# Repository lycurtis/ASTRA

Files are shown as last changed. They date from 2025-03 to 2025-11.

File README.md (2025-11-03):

# ASTRA - Autonomous System for Tracking, Reconnaissance, and Assistance
An open-source UAV platform for search-and-rescue (SAR) that combines real-time human detection, waypoint navigation, and ground-station visualization


ASTRA

## Table of contents
- [What is ASTRA](#what-is-astra)
- [Core Capabilities](#core-capabilities) 
- [System Architecture (High Level)](#system-architecture-high-level)
- [Key Specs & Design Targets](#key-specs--design-targets)
- [Demos](#demos)
- [How It Works (Data Flow)](#how-it-works-data-flow)
- [Testing Highlights](#testing-highlights)
- [Team](#team)

## What is ASTRA?
ASTRA is a semi-autonomous quadrotor designed to improve SAR operations. It flies in versatile environments, detect humans on-board using AI, and relays detections + GPS coordinates to a ground station UI for immediate response. ASTRA is the better alternative as it is a targeted, low-cost research platform that bridges manual piloting and intelligent rescue tooling.

## Core Capabilities 
- `On-board computer vision (YOLOv8):` Real-time human detection (single class: person) driven by NVIDIA Jetson Orin Nano + Luxonis OAK-D-Lite depth camera.
- `Waypoint/simulated autonomy:` Routes planned in QGroundControl (Pixhawk 4/PX4 Firmware).
- `Live communication:` Detections and telemetry to the ground station over UDP/Wi-Fi; MavLink telemetry maintained over RF
- `Ground-station UI:` Camera feed, Google Maps GPS view (online) with Offline Mode feedback map when there's no internet

## System Architecture (High Level)
ASTRA is split into UAV and Ground station subsystems:
- **UAV:** Pixhawk 4 (flight), M10 GPS, OAK-D-LITE
- **Ground Station:** Python/Tkinter UI showing detections, map, and terminal telemetry; live stream via Flask
### Highlight
- GPS --> Jetson (Processing + CV) --> UDP --> UI
- RF telemetry is maintained in parallel
- I2C/USB/UART form the internal peripheral backbone, and UDP carries time-sensitive events

## Key Specs & Design Targets
- **Flight Path**: Waypoint navigation, 9-10 ft altitude, 5 mph parameter set
- **Range (control/telemetry):** ~427 ft effective radius (validated)
- **Vision performance:** 20-25 FPS camera output; <= 800 ms end-to-end latency target
- **Detection Range:** ~50 m (person)
- **Power/Weight:** 4S 3300 mAh LiPo; total takeoff weight ~2.5 kg (5.5 lb)
- **Alert cadence:** 2 Hz SOS updates on detection

## Demos
Project clips:
- Flight & platform overview: https://youtu.be/dsUHsBSHA0g
- Ground-station & detections: https://youtu.be/vNRCC04JXCo

## How It Works (Data Flow)
1. `astra.py` boots the pipeline on the Jetson
2. `human_detect.py` processes OAK-D-Lite frames w/ YOLOv8 and logs `DETECTED`/`NOT_DETECTED`
3. `sos_transmitter.py` tails the log and transmits detection state via UDP to the ground station at the configured IP:5005 (de-duped on state change)
4. `astraui.py` from the ground station receives UDP, renders camera, map, and terminal; includes an **Offline Mode** map when the internet is unavailable

## Testing Highlights
- **RF control range:** Stable up to ~427 ft (two environments)
- **UDP comms:** Transmitter and receiver validated; terminal shows “PERSON DETECTED” / “Searching for persons…” on packets
- **Latency & video:** Bounded queue eliminated stale frames and reduced perceived lag in the UI
- **EMI mitigation:** Camera + USB 3.0 near GPS caused lock loss; shielding, grounding, cable reroute, and ferrites restored stable lock
- **Prop selection:** 1147 props chosen for best balance of lift/stability vs. 1045/1245

## Team
### Benjamin Kim
Main: Computer Vision (YOLOv8), PersonID

### Curtis Ly
Main: Hardware, System Architect 

### Pryce Matsudaira
Main: User Interface, PersonID

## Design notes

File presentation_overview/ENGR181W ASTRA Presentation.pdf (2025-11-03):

# ASTRA

Benjamin Kim, Curtis Ly, Pryce Matsudaira

# The Autonomous System for

Tracking, Reconnaissance,

# and Assistance

## 1) Problem Statement

## 2) Objectives

## 5) Innovation & Technical Depth

## 3) Design Approach

## 6) Limitations & Future Work

## 4) Implementation & Results

# Table of Contents

- Delays can determine life and death

## 3) Real-World Impact

- Search and Rescue (SAR) in unpredictable environments
- Need quick detection and response
- SAR systems rely on manual input
- Response time puts humans at risk
- Robotic support for human rescuers
- Minimizes human effort & maximizes response efficiency

# Demand for Autonomous Rescue Detection

## 1) The Problem

2) Current Limitations | 4) Solution

- Real-Time human detection
- Maintain accuracy
- Autonomous navigation
- Transmit alert signal with low latency

# Goals and Objectives

Problem Identified | ASTRA Objectives
Slow Human Detection | YOLOv8
Latency | On-board AI processing
Manual Labor | QGroundControl Autonomy

# Hardware System Integration

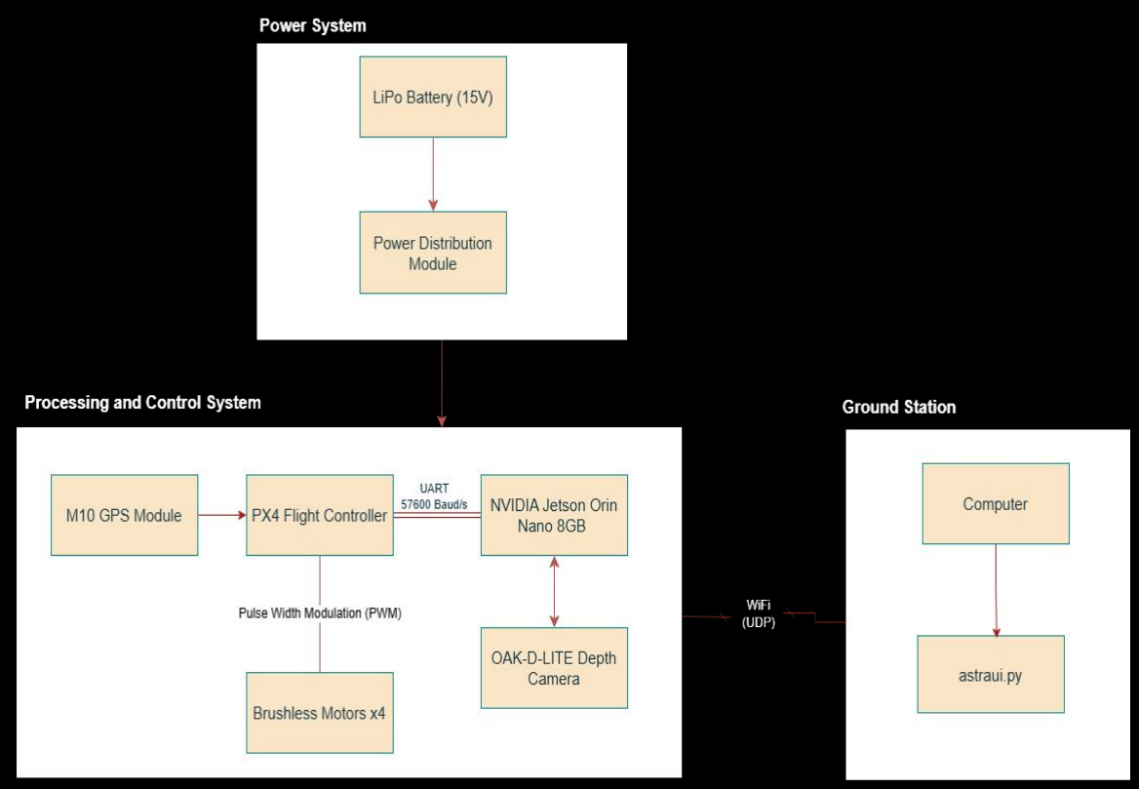
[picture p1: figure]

# Functionality

1) Power Distribution
2) Flight Control
3) Onboard Processing
4) Wireless Communication
5) Ground Station

# Software System Integration

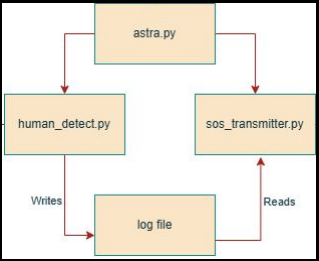
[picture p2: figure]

## Methodology Process

## 1) Object Detection Selection

## 4) Test and Improve

## 2) Vision Pipeline Integration

## 5) Final Integration

## 3) Communication Interface

### - UAV followed predefined routes

# Implementation & Results

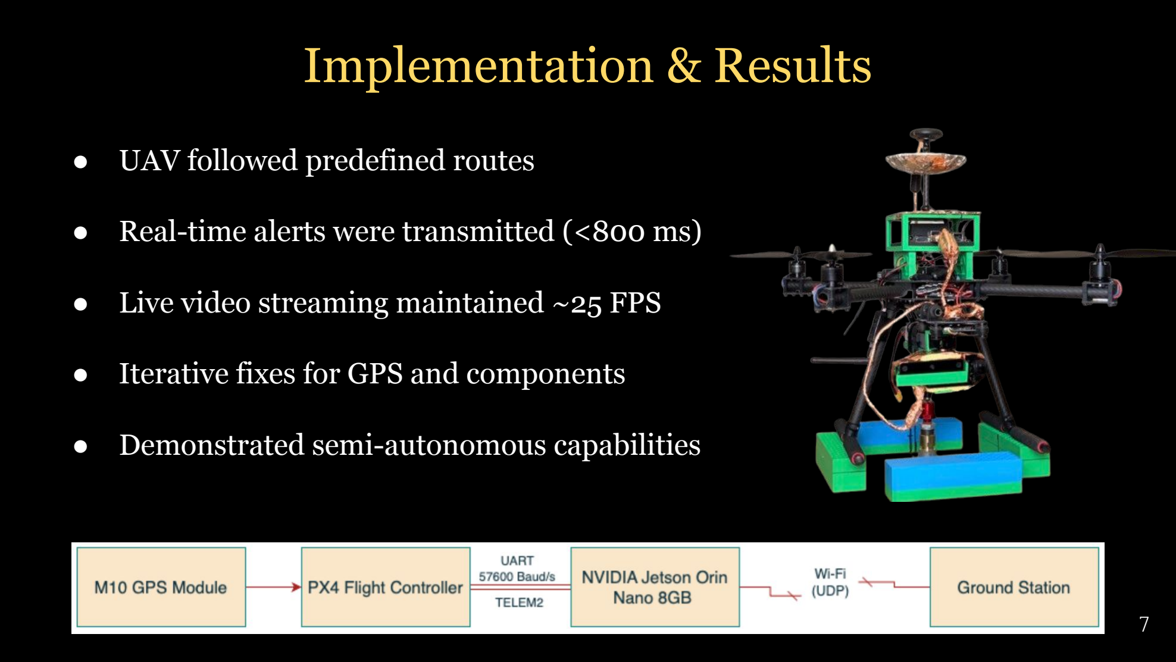
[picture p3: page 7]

### - Real-time alerts were transmitted (<800 ms)

### - Live video streaming maintained ~25 FPS

### - Iterative fixes for GPS and components

### - Demonstrated semi-autonomous capabilities

## - Improve video latency and resolution

## - Wi-Fi Dependency Workaround

## - Integrate Person Differentiation

## - Implement full autonomy

## - Flight Duration

# Limitations & Future Work

# Thank you

Benjamin Kim, Curtis Ly, Pryce Matsudaira

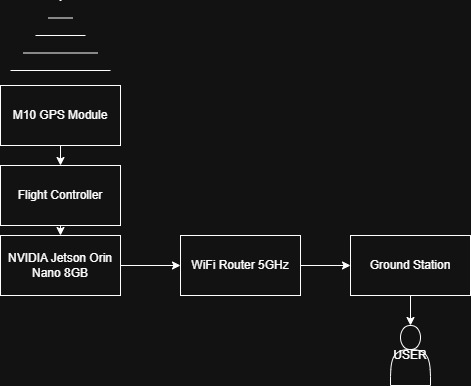
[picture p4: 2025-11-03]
system_charts/HighLevelArchitecture.jpg

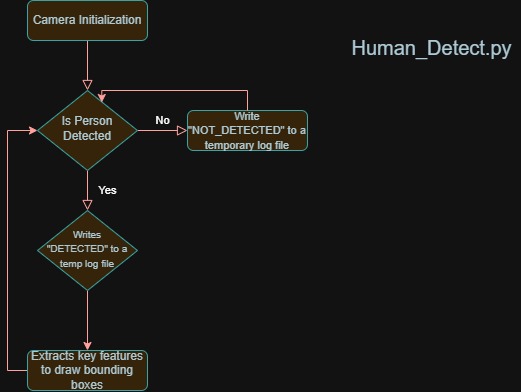
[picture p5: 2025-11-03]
system_charts/HumanDetect.py.jpg

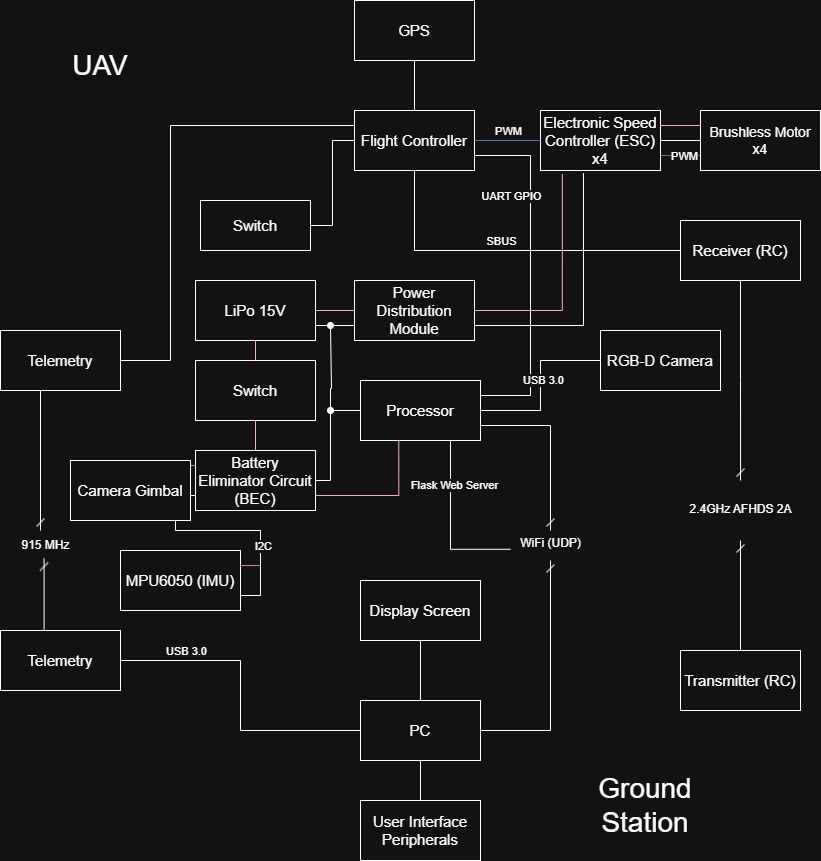
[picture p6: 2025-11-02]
system_charts/SystemBlockDiagram.jpg

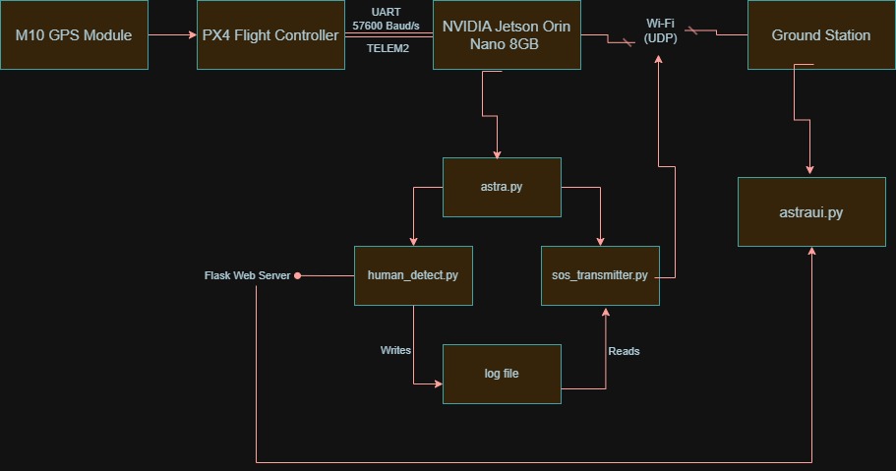
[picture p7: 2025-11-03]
system_charts/Functional_Flowchart.jpg

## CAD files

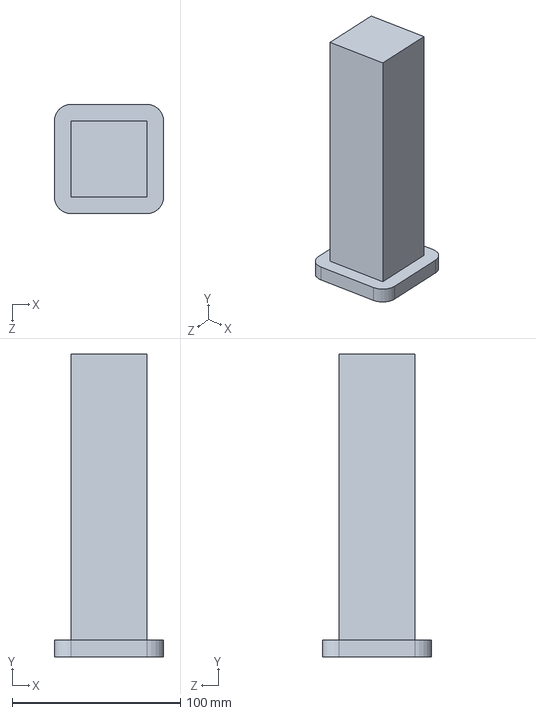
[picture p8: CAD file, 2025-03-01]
CAD/motor_level/motor_level_fullstand.SLDPRT
65.0 x 180.0 x 65.0 mm

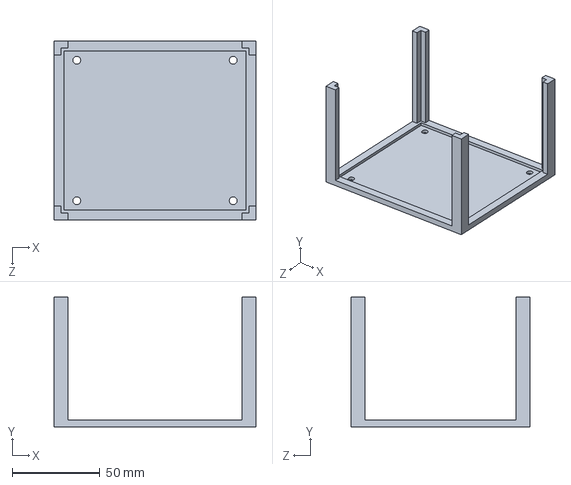
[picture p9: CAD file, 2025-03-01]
CAD/jetson/Jetson and LiDAR mount.SLDPRT
115.0 x 74.0 x 102.0 mm

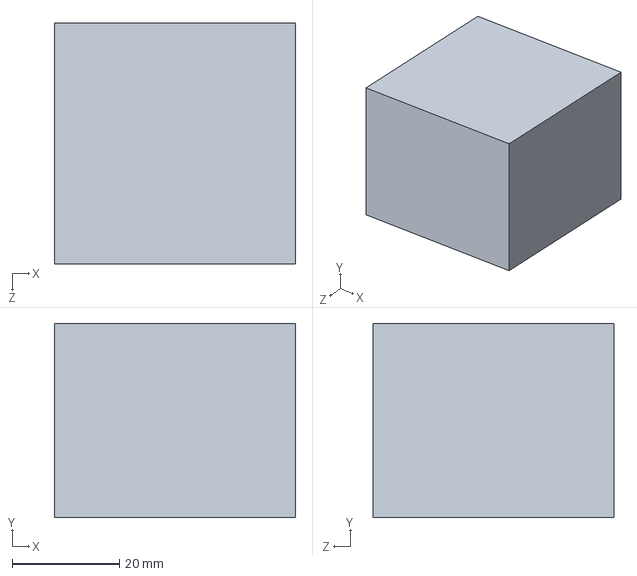
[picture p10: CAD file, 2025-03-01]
CAD/motor_level/2.SLDPRT
45.0 x 36.3 x 45.0 mm

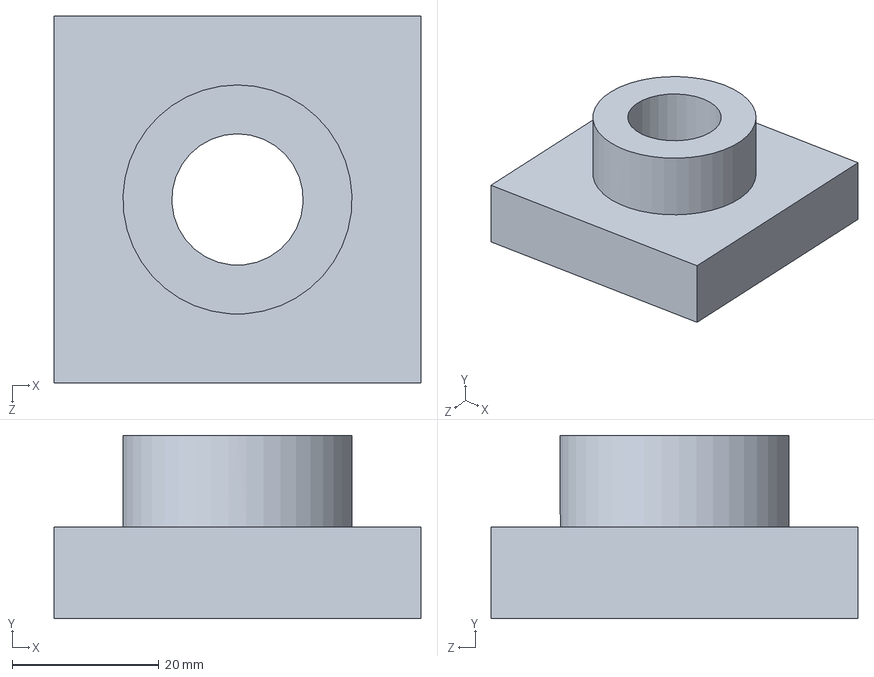
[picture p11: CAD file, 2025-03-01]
CAD/test_rig/testrigslot.SLDPRT
50.0 x 25.0 x 50.0 mm

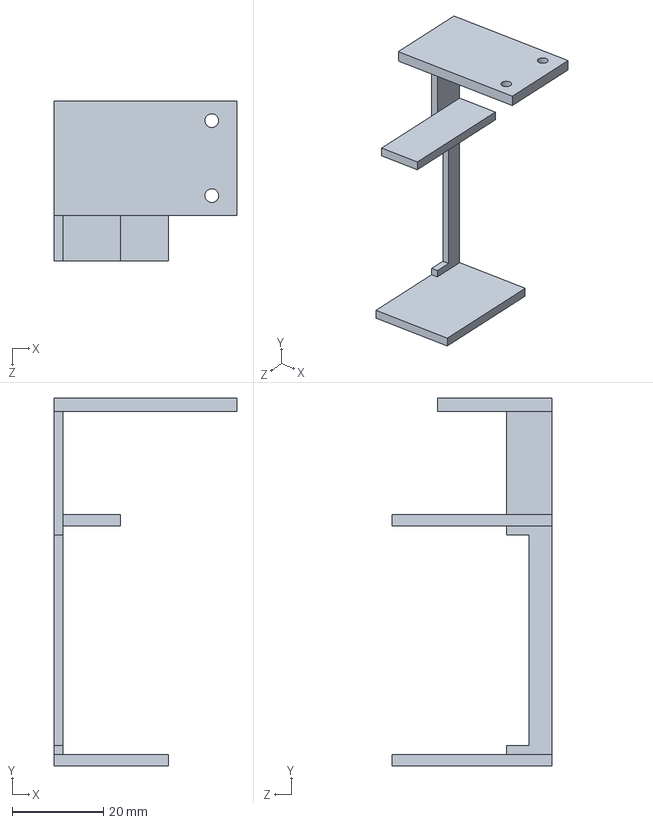
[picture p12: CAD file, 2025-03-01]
CAD/jetson/Gimbal Support.SLDPRT
40.0 x 80.5 x 35.0 mm

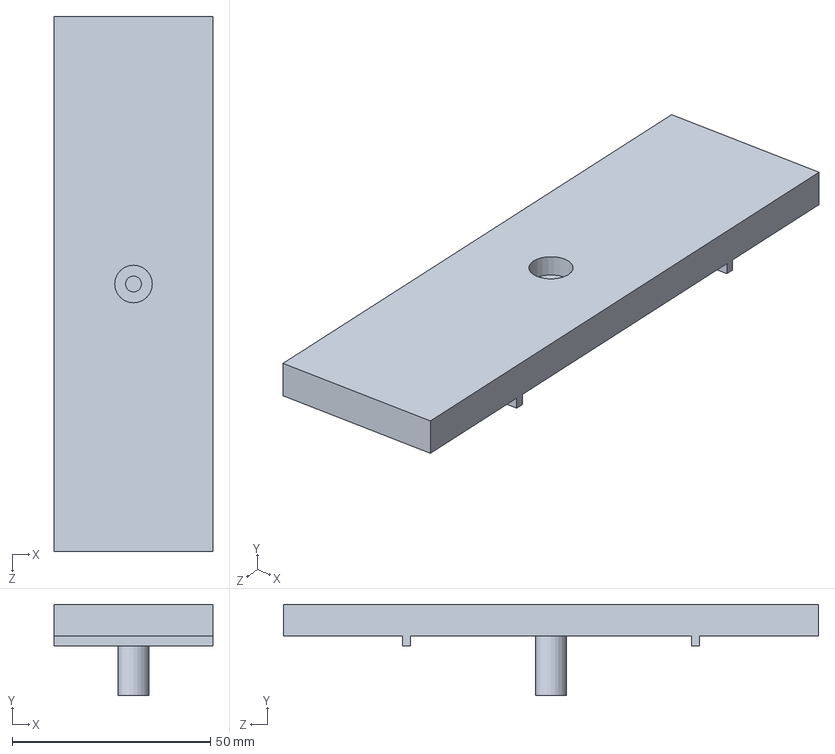
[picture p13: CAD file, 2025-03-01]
CAD/test_rig/ball swivel attachment.SLDPRT
40.0 x 23.0 x 135.0 mm

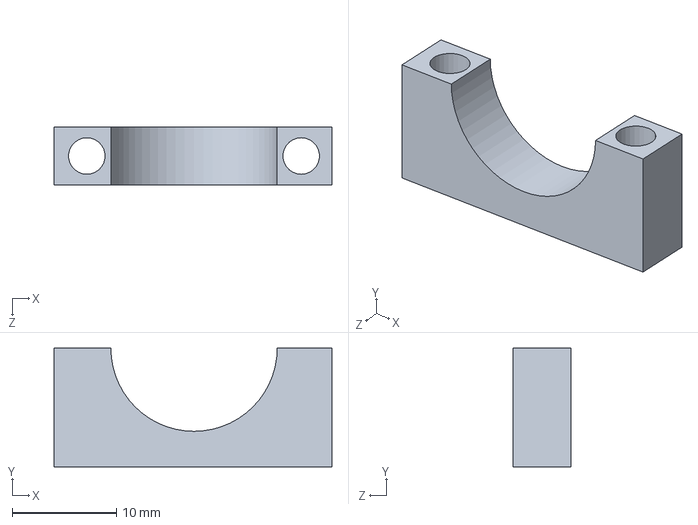
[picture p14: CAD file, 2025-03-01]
CAD/jetson/Arm Strap.SLDPRT
26.6 x 11.4 x 5.52 mm

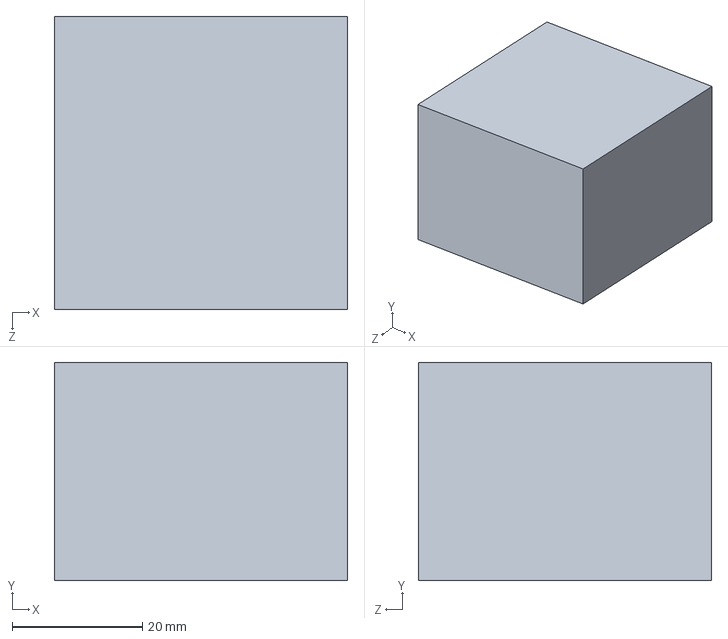
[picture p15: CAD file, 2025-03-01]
CAD/motor_level/motor_level_attachment.SLDPRT
45.0 x 33.5 x 45.0 mm

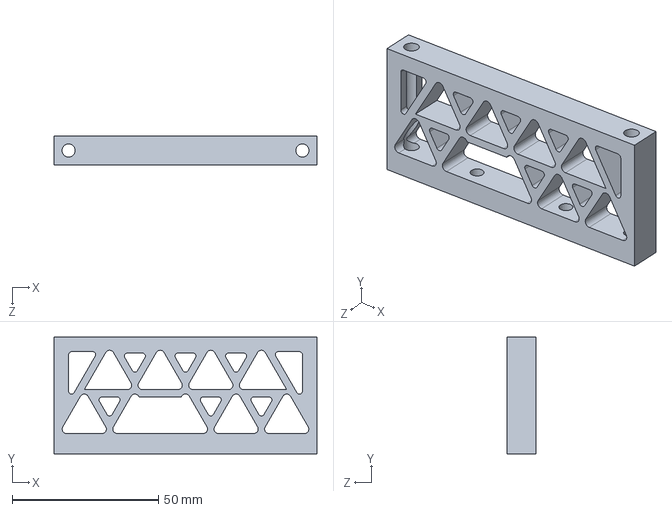
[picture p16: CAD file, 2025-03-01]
CAD/jetson/leg.SLDPRT
90.0 x 40.0 x 10.0 mm

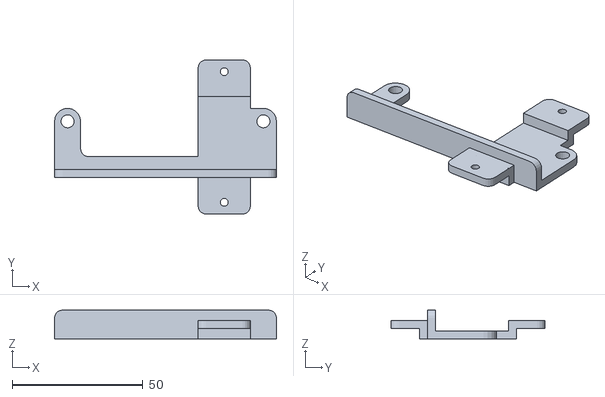
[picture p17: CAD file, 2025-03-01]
CAD/jetson/OAK-D Lite Gimbal Mount.stl
85.0 x 59.0 x 11.0

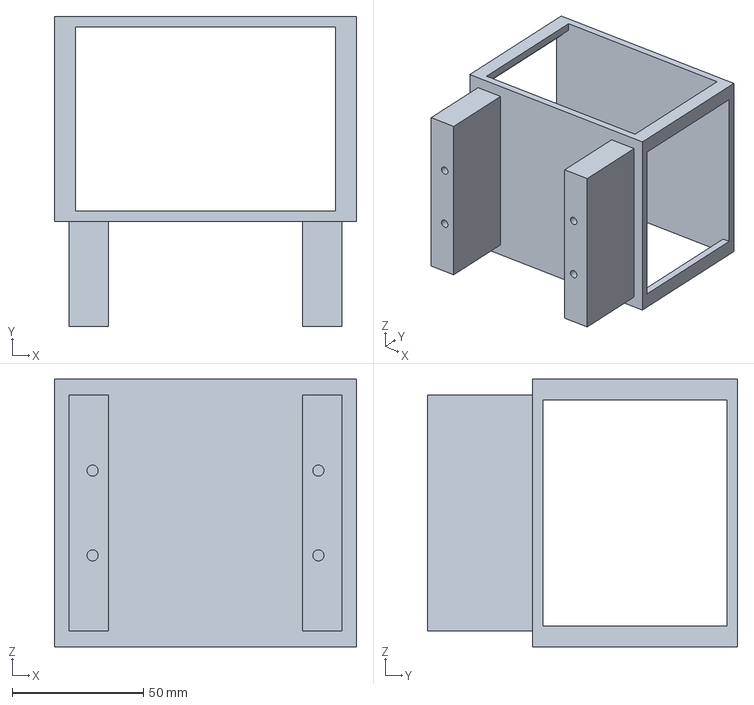
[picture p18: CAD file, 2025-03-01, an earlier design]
CAD/jetson/archive/Jetson and LiDAR mount.3MF
115.0 x 118.0 x 102.0 mm

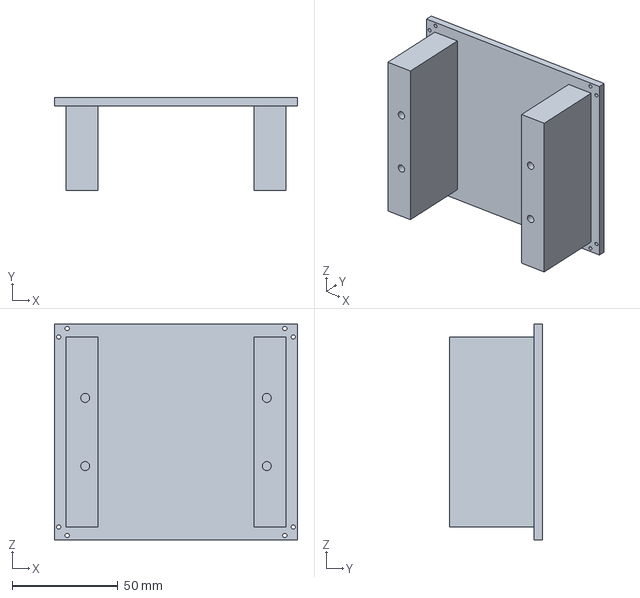
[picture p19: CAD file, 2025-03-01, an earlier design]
CAD/jetson/archive/Jetson mount.3MF
115.0 x 44.0 x 102.0 mm

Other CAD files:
CAD/jetson/archive/LiDAR mount.SLDPRT
CAD/jetson/Arm Strap.3MF
CAD/jetson/Gimbal Support.3MF
CAD/jetson/archive/LiDAR mount.3MF
CAD/jetson/leg.3MF
CAD/motor_level/2.3MF
CAD/motor_level/motor_level_attachment.3MF
CAD/motor_level/motor_level_fullstand.3MF
CAD/test_rig/ball swivel attachment.3MF
CAD/test_rig/testrigslot.3MF

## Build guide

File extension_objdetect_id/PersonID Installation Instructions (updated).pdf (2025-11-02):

# GPU-Accelerated Human Differentiation Network

Pryce Matsudaira & Benjamin Kim

Project Overview
This project implements a real-time detection and identification system for specific individuals. ASTRA (our senior design drone project) detects all people in a video feed using a pre-trained YOLOv8 model. The core objective of this project is to extend ASTRA’s scope to accurately detect specific people in a video stream and differentiate them by comparing visual features to a gallery of precomputed identity embeddings. To achieve this, we utilized a fine-tuned ResNet18 system for generating person-specific vector embeddings. Cosine similarity (via a custom CUDA kernel) is then used to compare those embeddings with a vector that represents the individual (e.x, differentiating between Ben and Pryce).

How the GPU is Used to Accelerate the Application
The GPU is used to accelerate the cosine similarity computation. When an individual is detected by a web camera, their ResNet18-generated feature vector is compared with a gallery of that individual’s stored embeddings. To make this comparison process efficient, a custom CUDA kernel is used to parallelize the cosine similarity calculations.
Our parallel algorithm is structured so that the query embedding is compared against all gallery embeddings at the same time. Each GPU thread computes the cosine similarity between those two vectors. Additionally, each thread also computes the similarity score for one gallery embedding, with 256 threads in one thread block. To ensure all gallery embeddings are executed, the grid size is set as the ceiling of the number of gallery embeddings divided by the thread block size. This allows for the similarity scores of N gallery embeddings to be computed in parallel within one kernel launch. The person identification stage of the software pipeline is parallelized.

Implementation Details
Each team member recorded two videos of themselves: one focused on their face (close-up) and another focused on their entire body. OpenCV was then used to extract frames from the videos at 5-frame intervals. Of those frames, the 10 best lighting and resolution images were manually selected and processed through a ResNet18 embedding model to extract a 512-dimensional feature vector. The vectors for each individual were averaged to create a gallery embedding for later use.

The implementation process of human_differentiation.py begins with real-time human detection via a YOLOv8 object detection algorithm, which had to be re-implemented for a desktop or laptop webcam through OpenCV. This was because the previous implementation for YOLOv8 on ASTRA relied on the compatibility with the drone’s depth camera drivers through Linux. Frames from a web camera will pass through YOLOv8 and output bounding boxes around detected humans. YOLOv8 will use such bounding boxes to crop regions of the detected individual and pass them through a pretrained ResNet18 model. The model will output a 512-dimensional feature vector of the individual’s visual features.
The script then ideally loads a compiled Parallel Thread Execution file with a CUDA kernel for efficient and fast cosine similarity computation. However, due to complications discussed later, the cosine similarity kernel had to be created and directly implemented in the human_differentiation.py script using Numba. A ResNet18 model is initialized as somewhat of an embedding extractor and deployed on the GPU. As mentioned earlier, Pryce and Ben each have stored image embeddings, which are loaded and organized into a NumPy array.
When a human is detected from the web camera, a ResNet18 model analyzes a cropped region of the detected individual and converts it into a 512-dimensional embedding vector. This vector analyzes the visual features of the individual and compares them against precomputed averaged embeddings using cosine similarity. Each thread calculates similarities between the ResNet18 embedding and the gallery embedding, allowing one-vs-many comparisons in a kernel launch.
If the calculated similarity score is higher than the defined threshold of 0.55 or 55%, the system will label the predicted human accordingly above their bounding box. If no match was detected, the system will label “Unknown Person”. This human differentiating system utilizes deep learning models, computer vision algorithms, and GPU acceleration to detect and label individuals.

Installation/Setup Process
1) Install Python (3.12 or higher) and required libraries, including opencv-python, numpy, numba, torch, cuda-python, torch, pillow, and ultralytics. Additionally, make sure the NVIDIA CUDA Toolkit (12.9) is installed and that NVIDIA GPU drivers are up to date.

2) First, upload video files of yourself and the people you want to differentiate to Google Drive. (Ex. My Drive → person_videos → pryce, ben)
a) Google Drive was mainly used to store datasets and videos for this project due to compatibility issues with each script on respective laptops/desktops. Not all laptops/desktops have the same file paths C:\User\etc\etc, which would require us to change the code every time to create dataset updates. Google Drive also allows you to share these videos and datasets easily
b) Example Image(s):

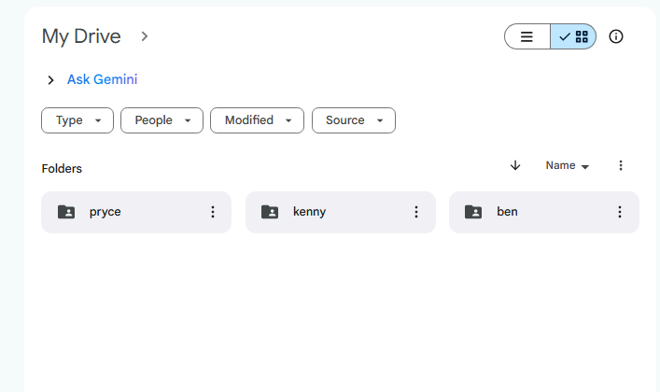
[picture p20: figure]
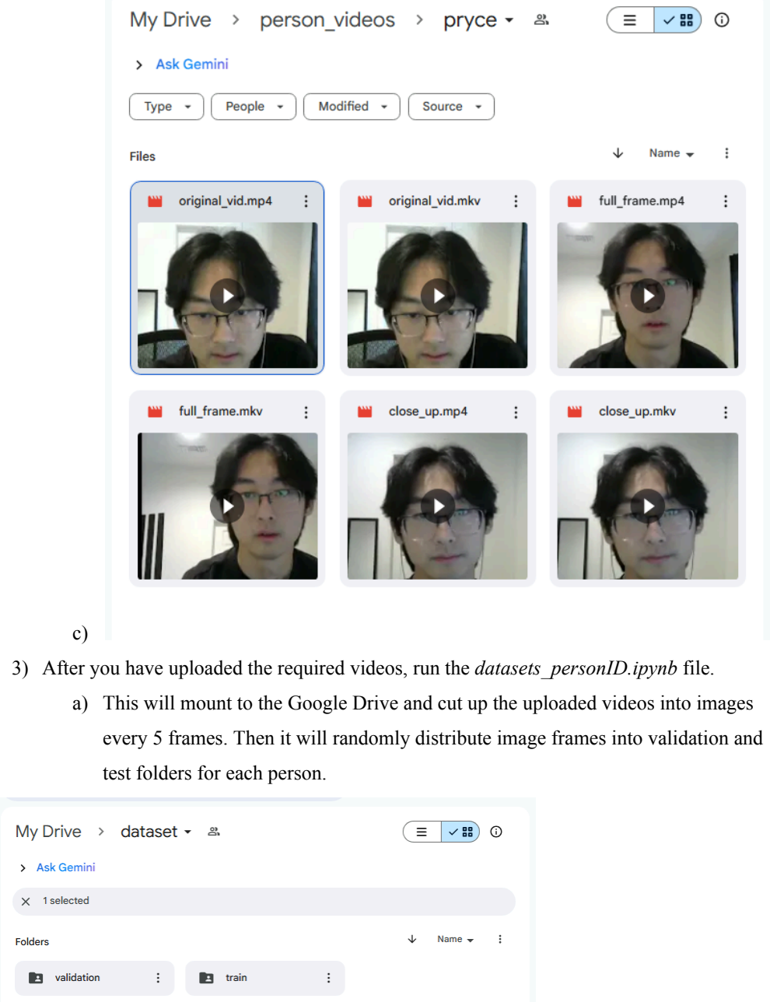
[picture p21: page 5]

c)
3) After you have uploaded the required videos, run the datasets_personID.ipynb file.
a) This will mount to the Google Drive and cut up the uploaded videos into images every 5 frames. Then it will randomly distribute image frames into validation and test folders for each person.

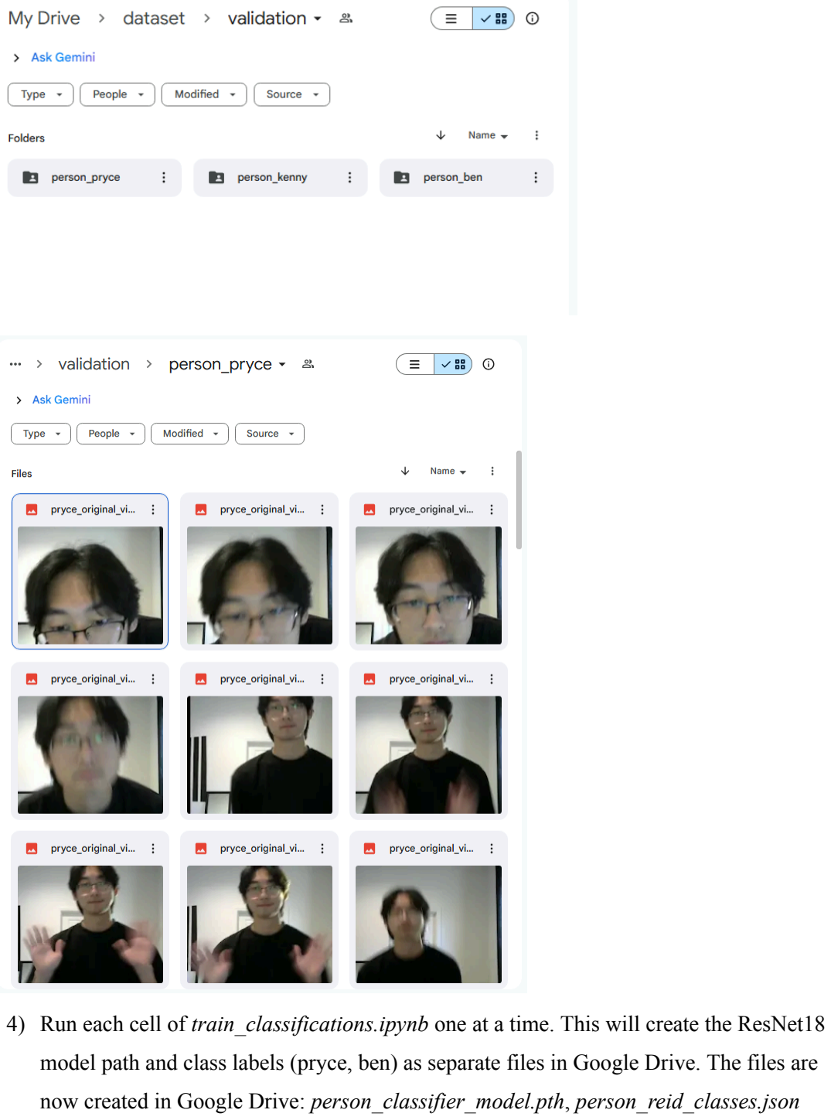
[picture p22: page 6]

4) Run each cell of train_classifications.ipynb one at a time. This will create the ResNet18 model path and class labels (pryce, ben) as separate files in Google Drive. The files are now created in Google Drive: person_classifier_model.pth, person_reid_classes.json a) Each cell will set up the classifier, loss function, and optimizer for classification, training loop, then classification model training (Epochs train loss/accuracy and validation loss)
5) Run each cell one at a time for embeddings_personID.ipynb. This file will begin building the ResNet18 model and initializing previously created weights. It will then extract features into a vector embedding. You will then test the shape and viability of the extracted embedding.
a) You will then manually input each image name from the validation folder “ben_IMG_7093_frame_00370.jpg” 10 times for each person you want to create an average embedding vector of.
6) You will then need to take person_classifier_model.pth and person_reid_classes.json files from Google Drive and import them to your specific computer.
7) Ensure folders and files are organized for proper file paths
- models/ (ResNet18 Models)
- person_classifier_model.pth
- person_reid_classes.json
- gallery_embeddings/ (Averaged embeddings of specific individuals from embeddings_personID.ipynb)
- ben_gallery_embedding.npy
- pryce_gallery_embedding.npy
- scripts/
- yolov8n.pt
Example Image:
8) Make sure to have your Python (3.12+) installation in the same directory as human_differentiation.py

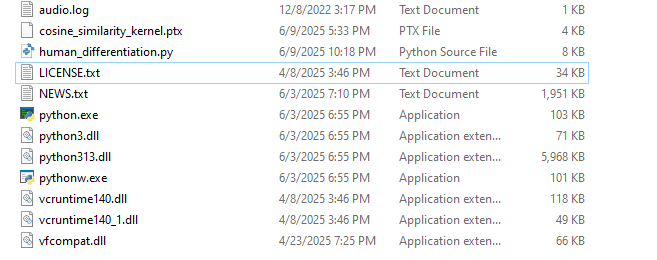
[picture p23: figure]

9) Make sure cosine_similarity_kernel.cu is in the PersonID folder or in a file that has administrator access. Now convert cosine_similarity_kernel.cu to a PTX file.
a) Open Developer Command Prompt for VS 2022 then input cd C:\YourPath\PersonID —> nvcc -ptx -ccbin "C:\Your\Full\Path\To\MSVC\bin\Hostx64\x64" cosine_similarity_kernel.cu -o cosine_similarity_kernel.ptx
b) A cosine_similarity_kernel.ptx file should now appear in the PersonID folder. Drag that to the same directory as human_differentiation.py
10) Run “python human_differentiation.py” in the command prompt of Visual Studio Code
11) If the cosine similarity kernel refuses to work with human_differentiation.py (like us). Error Statement: ‘cuda.cudart’ has no attribute ‘cuInit’
a) You will have to run the newly modified human_differentiation.py using Numba that directly implements the cosine_similarity_kernel and fulfills the project goal.
12) Run “python human_differentiation.py” in the command prompt of Visual Studio Code
13) Press “q” to quit

Demo Video
Link: https://youtu.be/pVjVxKaa4ik

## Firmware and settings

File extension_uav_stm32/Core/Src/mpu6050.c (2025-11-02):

#include "mpu6050.h"
#include "i2c.h"


//void MPU6050_Init(void){
//	uint8_t data = 0x00; // Wake up device
//	I2C_Mem_Write(MPU6050_I2C_ADDR, MPUR_PWR_MGMT_1, &data, 1);
//}


// Calibration offsets
static int16_t accel_x_offset = 0, accel_y_offset = 0, accel_z_offset = 0;
static int16_t gyro_x_offset = 0, gyro_y_offset = 0, gyro_z_offset = 0;

uint8_t MPU6050_Init(void){
	uint8_t check;
	uint8_t data;

	//Initialize the I2C peripheral
	//I2C_Init(); //Optional placement here or place in main file

	//Check the WHO_AM_I register to confirm communication with the MPU6050
	//The MPU6050's I2C address is 0x68, therefore this register should also contain 0x68
	I2C_Mem_Read(MPU6050_I2C_ADDR, MPU6050_WHO_AM_I, &check, 1);

	if(check == MPU6050_I2C_ADDR){
		//Must wake up device by writing 0 to the Power Management 1 Register
		data = 0x00;
		I2C_Mem_Write(MPU6050_I2C_ADDR, MPUR_PWR_MGMT_1, &data, 1);

		// Set the sample rate. 1kHz/(1+SMPLRT_DIV)
		// Set SMPLRT_DIV to 7 for a 125Hz sample rate
		data = 0x07;
		I2C_Mem_Write(MPU6050_I2C_ADDR, MPUR_SMPLRT_DIV, &data, 1);

		// Configure the accelerometer to a full-scale range of +/- 2g
		data = 0x00;
		I2C_Mem_Write(MPU6050_I2C_ADDR, MPUR_ACCEL_CONFIG, &data, 1);

		// Configure the gyroscope to a full-scale range of +/- 250 degrees/sec
		data = 0x00;
		I2C_Mem_Write(MPU6050_I2C_ADDR, MPUR_GYRO_CONFIG, &data, 1);

		return 1; // success
	}

	return 0; // fail
}

void MPU6050_Read_Accel(int16_t *accel_x, int16_t * accel_y, int16_t *accel_z){
	uint8_t buffer[6]; //stores raw data

	// Read 6 bytes of data starting from the ACCEL_XOUT_H register
	// Note: The MPU will automatically increment the register address after each read
	I2C_Mem_Read(MPU6050_I2C_ADDR, MPUR_ACCEL_XOUT_H, buffer, 6);

	// data is transmitted in big-endian format (MSB first)
	// we combine the high and low bytes for each axis to form a 16-bit signed integer
	*accel_x = (int16_t)(buffer[0] << 8 | buffer[1]);
	*accel_y = (int16_t)(buffer[2] << 8 | buffer[3]);
	*accel_z = (int16_t)(buffer[4] << 8 | buffer[5]);
}

void MPU6050_Read_Gyro(int16_t *gyro_x, int16_t *gyro_y, int16_t *gyro_z){
	uint8_t buffer[6];

	I2C_Mem_Read(MPU6050_I2C_ADDR, MPUR_GYRO_XOUT_H, buffer, 6);

	*gyro_x = (int16_t)(buffer[0] << 8 | buffer[1]);
	*gyro_y = (int16_t)(buffer[2] << 8 | buffer[3]);
	*gyro_z = (int16_t)(buffer[4] << 8 | buffer[5]);
}


void MPU6050_Calibrate(void){
	// Calibrate accel
	int32_t sum_x = 0, sum_y = 0, sum_z = 0;
	const int samples = 500;
	for (int i = 0; i < samples; i++) {
		int16_t ax, ay, az;
		MPU6050_Read_Accel(&ax, &ay, &az);
		sum_x += ax;
		sum_y += ay;
		sum_z += az;
	}
	accel_x_offset = sum_x / samples;
	accel_y_offset = sum_y / samples;
	accel_z_offset = (sum_z / samples) - 16384; // Optional: subtract 16384 if you want "0g at rest"

	// Calibrate gyro
	sum_x = sum_y = sum_z = 0;
	for (int i = 0; i < samples; i++) {
		int16_t gx, gy, gz;
		MPU6050_Read_Gyro(&gx, &gy, &gz);
		sum_x += gx;
		sum_y += gy;
		sum_z += gz;
	}
	gyro_x_offset = sum_x / samples;
	gyro_y_offset = sum_y / samples;
	gyro_z_offset = sum_z / samples;
}


void MPU6050_Read_Calibrated(float *ax_g_out, float *ay_g_out, float *az_g_out, float *gx_dps_out, float *gy_dps_out, float *gz_dps_out){
	 int16_t accel_x, accel_y, accel_z;
	    int16_t gyro_x, gyro_y, gyro_z;

	    MPU6050_Read_Accel(&accel_x, &accel_y, &accel_z);
	    MPU6050_Read_Gyro(&gyro_x, &gyro_y, &gyro_z);

	    // Offset correction
	    int16_t axc = accel_x - accel_x_offset;
	    int16_t ayc = accel_y - accel_y_offset;
	    int16_t azc = accel_z - accel_z_offset;

	    int16_t gxc = gyro_x - gyro_x_offset;
	    int16_t gyc = gyro_y - gyro_y_offset;
	    int16_t gzc = gyro_z - gyro_z_offset;

	    // Normalization
	    *ax_g_out = axc / 16384.0f;
	    *ay_g_out = ayc / 16384.0f;
	    *az_g_out = azc / 16384.0f;

	    *gx_dps_out = gxc / 131.0f;
	    *gy_dps_out = gyc / 131.0f;
	    *gz_dps_out = gzc / 131.0f;
}
